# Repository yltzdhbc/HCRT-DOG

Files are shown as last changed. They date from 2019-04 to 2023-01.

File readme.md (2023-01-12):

# 【开源四足机器人】 HCRT-DOG

Jump

**本项目是一个并联式的四足机器人 每条腿使用了两个电机驱动共四条腿，八个电机期望实现四种步态，从慢到快依次为，行进步态（三足支撑）、小跑步态（两拍步态）、溜蹄步态、疾驰步态。**

---

>该软件遵循MIT开源协议，作者保留版权，无任何其他限制，但是你必须在你的软件中包含原MIT授权协议的声明。由于本人时间、能力有限，有许多不足之处，欢迎在GitHub的`Issues`中留言

更多信息请访问：

我的博客：https://yltzdhbc.top/HCRT-DOG

github: https://github.com/yltzdhbc/HCRT-DOG

gitee: https://gitee.com/yltzdhbc/HCRT-DOG

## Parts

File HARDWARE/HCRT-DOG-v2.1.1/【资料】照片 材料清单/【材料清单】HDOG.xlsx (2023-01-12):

序号 | 材料名称 | SW零件标注 | 型号 | 单价（元/个） | 数量（个） | 金额（元） | 备注 | 链接
1 | 塞打螺丝 | 【塞打螺丝】M10-16 | 光杆直径：10mm 光杆长度：16mm 螺纹直径：M8 | 3.95 | 3 | 11.85 |  | https://item.taobao.com/item.htm?spm=a1z10.3-c-s.w4002-17447720939.19.30d73951rLTWwY&id=13899628761
2 | 深沟球轴承 | 【深沟球轴承】6800ZZ 尺寸：10-19-5 | 内径：10mm 外径：19mm 厚度：5mm | 1.4 | 6 | 8.4 |  | https://item.taobao.com/item.htm?spm=a1z10.3-c-s.w4002-17447720939.14.1cba3951MBdidW&id=12451607060
3 | 平面推力滚针轴承 | 【平面推力滚针轴承】尺寸：10-24-4 | 内径：10mm 外径：24mm 厚度：4mm | 2.16 | 3 | 6.48 |  | https://detail.tmall.com/item.htm?id=586222233089&_u=v2mk2m4e0769&skuId=4149740695817
4 | 滑板轴承 | 【深沟球轴承】608ZZ 尺寸：8-22-7 | 内径：8mm 外径：22mm 厚度：7mm | 0.8 | 2 | 1.6 |  | https://item.taobao.com/item.htm?spm=a1z10.3-c-s.w4002-17447720939.12.10843951j3HL8x&id=10864775059
5 | 光轴

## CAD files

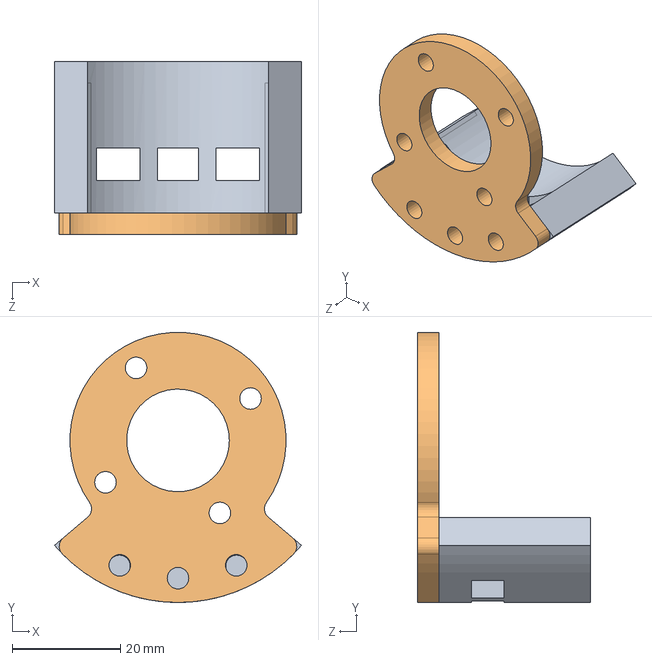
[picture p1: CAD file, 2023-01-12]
HARDWARE/HCRT-DOG-v2.1.1/B【部分装配】马蹄.SLDASM
45.7 x 50.0 x 32.0 mm
【马蹄结构件】蹄子底板
【马蹄结构件】蹄子侧板

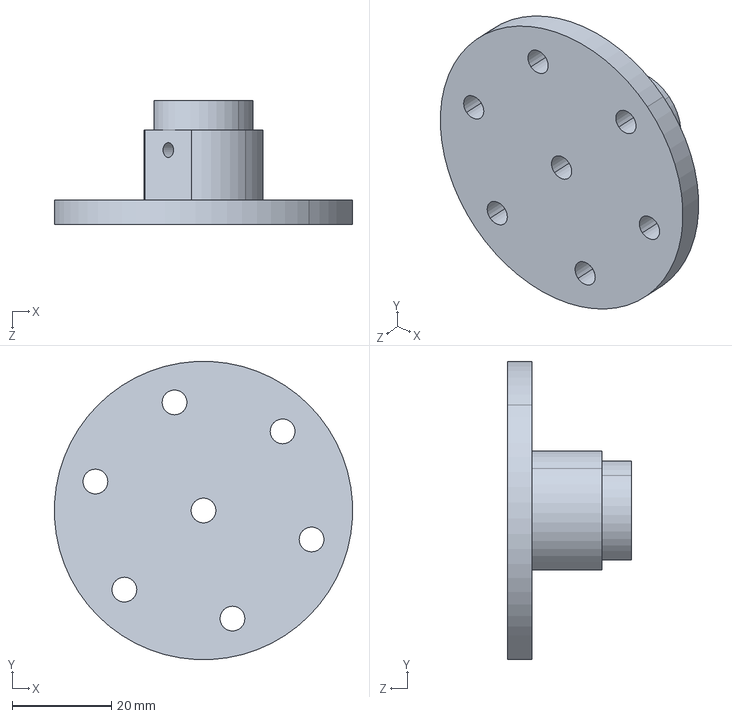
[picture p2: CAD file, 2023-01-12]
HARDWARE/HCRT-DOG-v2.1.1/【法兰联轴器】M10-孔3.SLDASM
59.9 x 59.9 x 25.0 mm

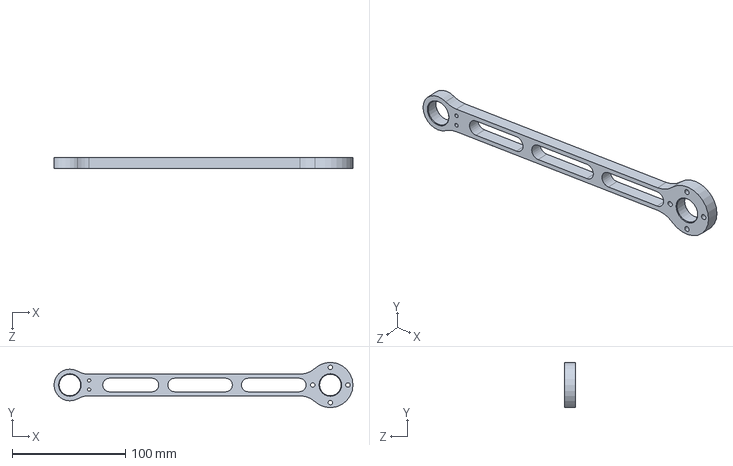
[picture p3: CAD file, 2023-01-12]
HARDWARE/HCRT-DOG-v2.1.1/【铝合金结构件】小腿2.SLDPRT
264.0 x 40.0 x 10.0 mm

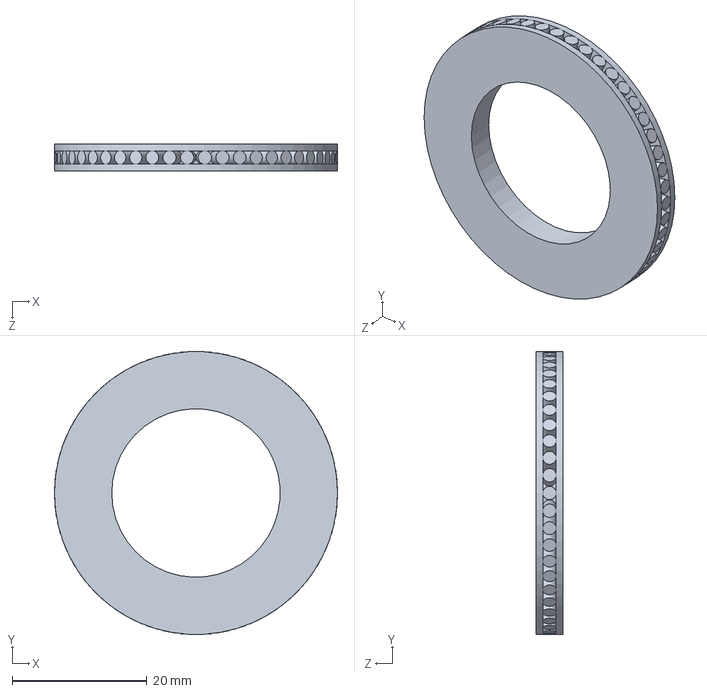
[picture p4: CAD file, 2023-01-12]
HARDWARE/HCRT-DOG-v2.1.1/【平面推力滚针轴承】尺寸：25-42-4.SLDPRT
42.0 x 42.0 x 4.00 mm

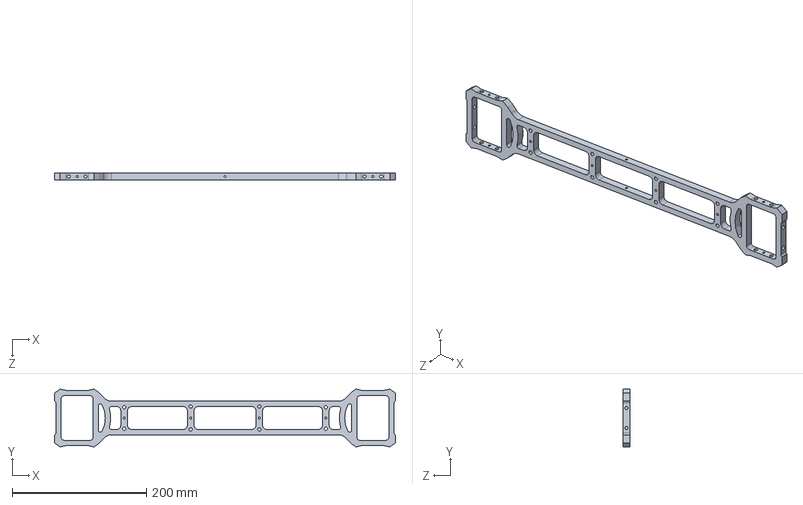
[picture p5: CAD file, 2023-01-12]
HARDWARE/HCRT-DOG-v2.1.1/【铝合金结构件】侧边铝板.SLDPRT
507.2 x 86.2 x 10.0 mm

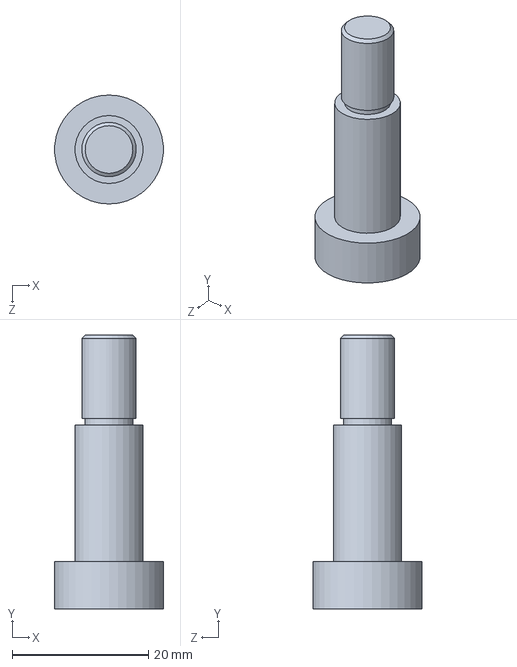
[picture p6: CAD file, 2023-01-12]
HARDWARE/HCRT-DOG-v2.1.1/【塞打螺丝】M10-20.SLDPRT
15.9 x 40.2 x 16.0 mm

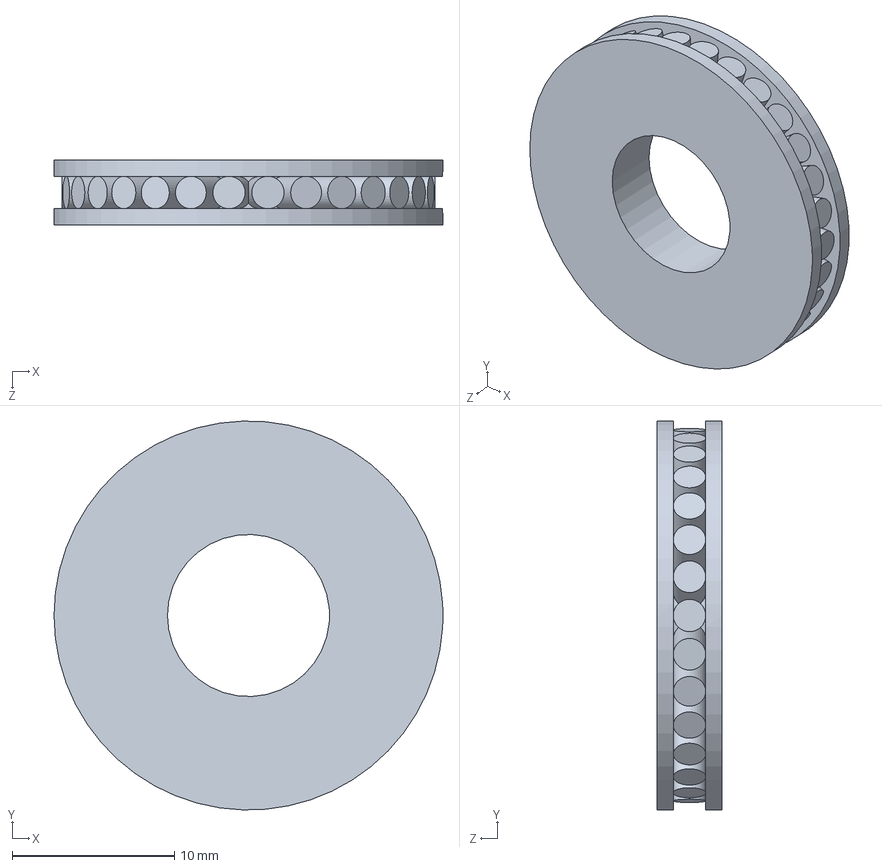
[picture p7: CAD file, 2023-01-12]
HARDWARE/HCRT-DOG-v2.1.1/【平面推力滚针轴承】尺寸：10-24-4.SLDPRT
24.0 x 24.0 x 4.00 mm

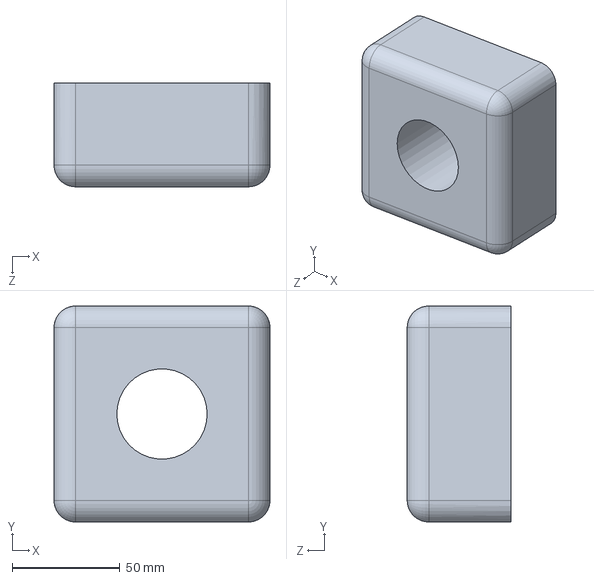
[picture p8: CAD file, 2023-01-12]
HARDWARE/HCRT-DOG-v2.1.1/【泡沫保护件】外侧电机保护泡沫.SLDPRT
100.0 x 100.0 x 48.0 mm

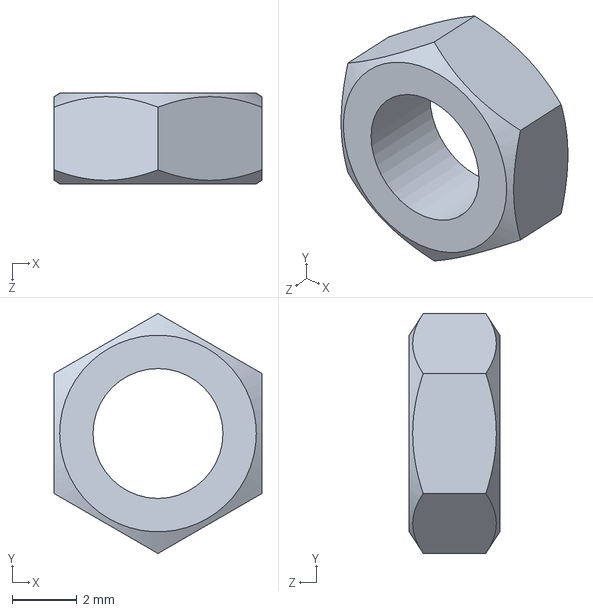
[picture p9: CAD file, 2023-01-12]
HARDWARE/HCRT-DOG-v2.1.1/【螺母】M4-2.8 普通六角螺母.SLDPRT
6.40 x 7.39 x 2.80 mm

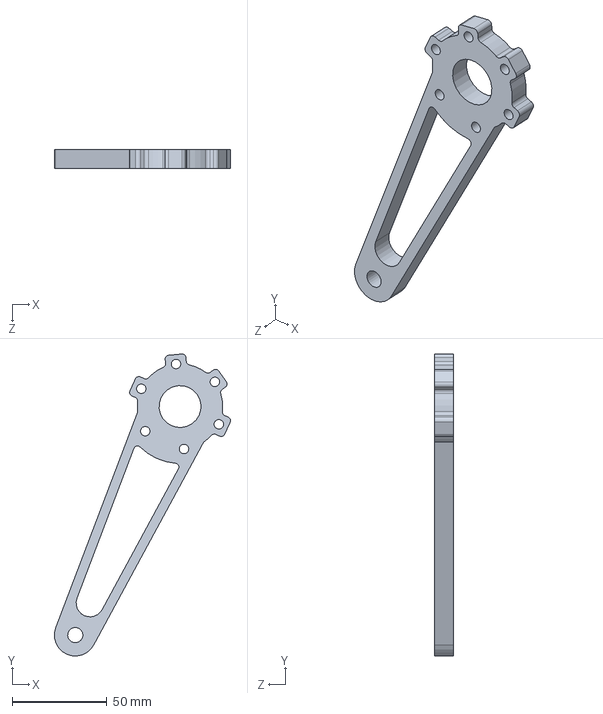
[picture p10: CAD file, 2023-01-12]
HARDWARE/HCRT-DOG-v2.1.1/【铝合金结构件】大腿.SLDPRT
92.9 x 159.3 x 10.0 mm

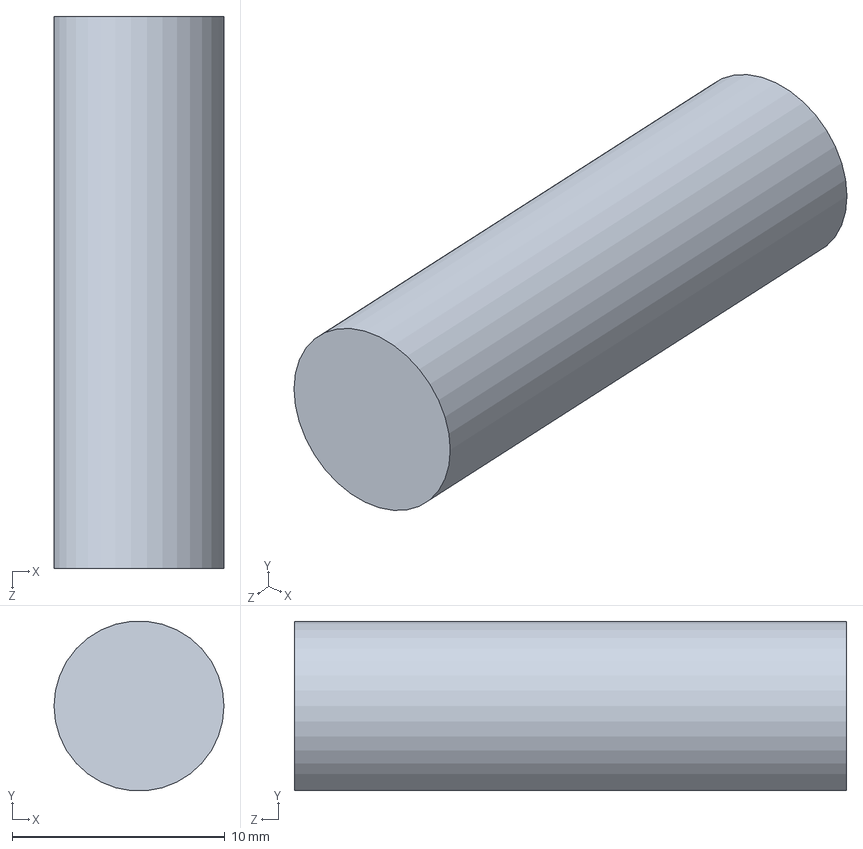
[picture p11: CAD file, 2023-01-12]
HARDWARE/HCRT-DOG-v2.1.1/【光杆】M8-26.SLDPRT
8.00 x 7.97 x 26.0 mm

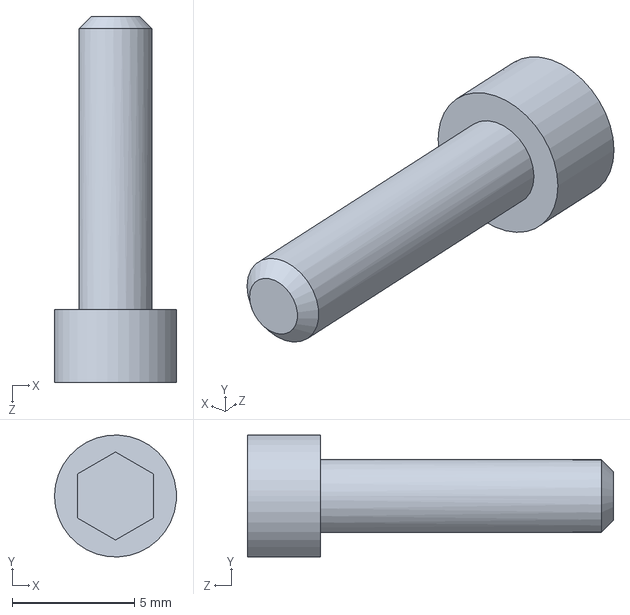
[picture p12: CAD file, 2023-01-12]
HARDWARE/HCRT-DOG-v2.1.1/【螺丝】M3-12 杯头内六角.SLDPRT
5.00 x 4.99 x 15.0 mm

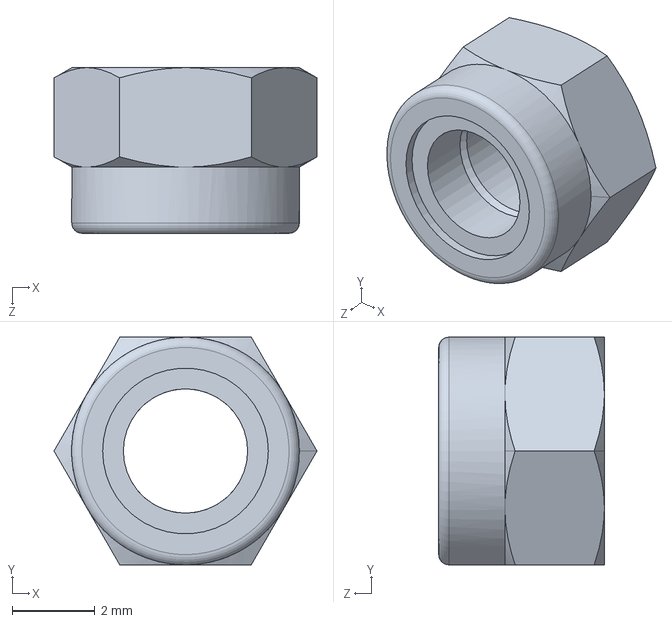
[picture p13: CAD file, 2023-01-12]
HARDWARE/HCRT-DOG-v2.1.1/【螺母】M3-4.0 自锁六角螺母 .SLDPRT
6.35 x 5.50 x 4.00 mm

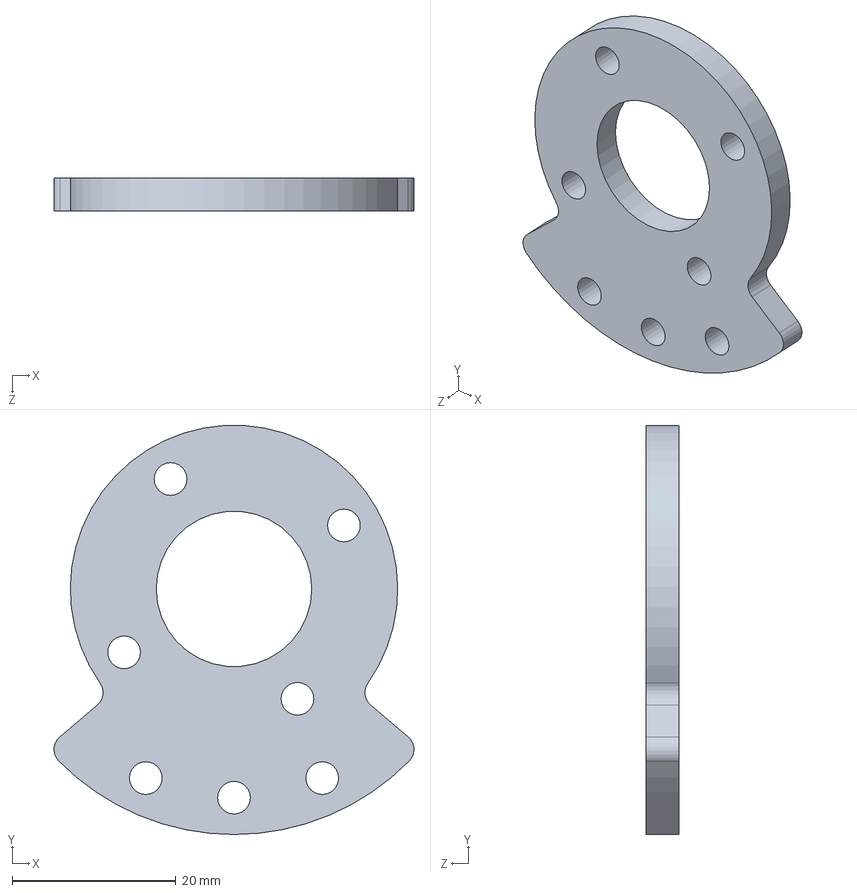
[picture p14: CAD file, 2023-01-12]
HARDWARE/HCRT-DOG-v2.1.1/【马蹄结构件】蹄子侧板.SLDPRT
44.0 x 50.0 x 4.00 mm

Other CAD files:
HARDWARE/HCRT-DOG-v2.1.1/【螺丝】M5-10 杯头内六角.SLDPRT
HARDWARE/HCRT-DOG-v2.1.1/【螺丝】M4-10 杯头内六角.SLDPRT
HARDWARE/HCRT-DOG-v2.1.1/【碳纤维板垫片】10-15-2.SLDPRT
HARDWARE/HCRT-DOG-v2.1.1/【螺丝】M3-22 杯头内六角.SLDPRT
HARDWARE/HCRT-DOG-v1.0.3/1.SLDASM
HARDWARE/HCRT-DOG-v1.0.3/10cm.SLDPRT
HARDWARE/HCRT-DOG-v1.0.3/2.SLDASM
HARDWARE/HCRT-DOG-v1.0.3/20-1.SLDPRT
HARDWARE/HCRT-DOG-v1.0.3/20cm.SLDPRT
HARDWARE/HCRT-DOG-v1.0.3/3508电机.SLDASM
HARDWARE/HCRT-DOG-v1.0.3/RM3508电机.sldprt
HARDWARE/HCRT-DOG-v1.0.3/减震橡胶.SLDPRT
HARDWARE/HCRT-DOG-v1.0.3/吸盘夹/changganjiachi.SLDPRT
HARDWARE/HCRT-DOG-v1.0.3/吸盘夹/一号彭磊机构总装.SLDASM
HARDWARE/HCRT-DOG-v1.0.3/吸盘夹/升降机构铝板.SLDPRT
HARDWARE/HCRT-DOG-v1.0.3/吸盘夹/吸盘.SLDPRT
HARDWARE/HCRT-DOG-v1.0.3/吸盘夹/吸盘夹.SLDASM
HARDWARE/HCRT-DOG-v1.0.3/吸盘夹/吸盘板.SLDPRT
HARDWARE/HCRT-DOG-v1.0.3/吸盘夹/吸盘板12个吸盘.DWG
HARDWARE/HCRT-DOG-v1.0.3/吸盘夹/吸盘，内径16.SLDASM
HARDWARE/HCRT-DOG-v1.0.3/吸盘夹/小细管.SLDPRT
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

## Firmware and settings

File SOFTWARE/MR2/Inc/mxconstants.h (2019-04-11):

/**
  ******************************************************************************
  * File Name          : mxconstants.h
  * Description        : This file contains the common defines of the application
  ******************************************************************************
  *
  * COPYRIGHT(c) 2017 STMicroelectronics
  *
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
  ******************************************************************************
  */
/* Define to prevent recursive inclusion -------------------------------------*/
#ifndef __MXCONSTANT_H
#define __MXCONSTANT_H
  /* Includes ------------------------------------------------------------------*/


#define IST_INT_Pin GPIO_PIN_3
#define IST_INT_GPIO_Port GPIOE
#define IST_RST_Pin GPIO_PIN_2
#define IST_RST_GPIO_Port GPIOE
#define IMU_HEAT_PWM_Pin GPIO_PIN_5
#define IMU_HEAT_PWM_GPIO_Port GPIOB
#define LASER_Pin GPIO_PIN_13
#define LASER_GPIO_Port GPIOG
#define BEEP_Pin GPIO_PIN_4
#define BEEP_GPIO_Port GPIOB
#define KEY1_Pin GPIO_PIN_7
#define KEY1_GPIO_Port GPIOD
#define KEY2_Pin GPIO_PIN_10
#define KEY2_GPIO_Port GPIOD
#define LED1_Pin GPIO_PIN_14
#define LED1_GPIO_Port GPIOF
#define LED2_Pin GPIO_PIN_7
#define LED2_GPIO_Port GPIOE
/**
  * @}
  */ 

/**
  * @}
*/ 

#endif /* __MXCONSTANT_H */
/************************ (C) COPYRIGHT STMicroelectronics *****END OF FILE****/

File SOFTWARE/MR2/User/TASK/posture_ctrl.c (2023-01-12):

#include "posture_ctrl.h"


float x, y, theta1, theta2;

enum States state = REALSE;

extern TaskHandle_t MotorControlTask_Handler;

float _angle_initial,_rotate_angle;

bool TurnLeftFlag1,TurnLeftFlag2,TurnRightFlag1,TurnRightFlag2,ClimbingFlag1,ClimbingFlag2;

bool _leg_active[4]= {1,1,1,1};

float now_time;

bool rc_ctrl_flag = 1;

//初始化步态增益
LegGain gait_gains = {15.5, 0.00, 25.0, 0.00};
//设定每一种步态的具体增益
LegGain state_gait_gains[] = {
    //{kp_pos, kd_pos} kp_spd, kd_spd,
    {22.0, 0.00, 8.0, 0.00},  //位置环 速度环 TROT
    {22.0, 0.00, 8.0, 0.00},  //TEST1
    {22.0, 0.00, 8.0, 0.00},
    {22.0, 0.00, 8.0, 0.00},
    {22.0, 0.00, 8.0, 0.00},
    {22.0, 0.00, 8.0, 0.00},
    {22.0, 0.00, 8.0, 0.00},
    {22.0, 0.00, 8.0, 0.00},
    {22.0, 0.00, 8.0, 0.00},
    {22.0, 0.00, 8.0, 0.00},
    {22.0, 0.00, 8.0, 0.00},
    {22.0, 0.00, 8.0, 0.00},
    {22.0, 0.00, 8.0, 0.00},  //TEST12
    {22.0, 0.00, 8.0, 0.00},  //CLIMB
    {22.0, 0.00, 8.0, 0.00},
    {22.0, 0.00, 8.0, 0.00},
    {22.0, 0.00, 8.0, 0.00},
    {22.0, 0.00, 8.0, 0.00},
    {22.0, 0.00, 8.0, 0.00},
    {22.0, 0.00, 8.0, 0.00},
    {22.0, 0.00, 8.0, 0.00}, //STOP
    {22.0, 0.00, 8.0, 0.00}, //REL
    {22.0, 0.00, 8.0, 0.00},
    {22.0, 0.00, 8.0, 0.00},
    {22.0, 0.00, 8.0, 0.00},
};


//初始化步态参数
GaitParams gait_params = {17.3,12.0,4.0,0.00,0.25,1};
//设定每一种步态的具体参数
GaitParams state_gait_params[] = {
    //{stance_height, step_length, up_amp, down_amp, flight_percent, freq}  cm
    //{步高, 步长, 抬腿高, 压腿高, 飞行占比, 频率}	单位 cm
    {16.0, 16.0, 5.00, 2.00, 0.25, 1.85}, // TROT	双拍步态 对角小跑
    {26.0, 10.00, 3, 2.00, 0.20, 2.0},//1
    {26.0, 10.00, 3, 2.00, 0.20, 2.0},//2
    {26.0, 10.00, 3, 2.00, 0.20, 2.0},//3
    {NAN, NAN, NAN, NAN, NAN, NAN},		//4
    {NAN, NAN, NAN, NAN, NAN, NAN},		//5
    {NAN, NAN, NAN, NAN, NAN, NAN},		//6
    {NAN, NAN, NAN, NAN, NAN, NAN},		//7
    {NAN, NAN, NAN, NAN, NAN, NAN},		//8
    {NAN, NAN, NAN, NAN, NAN, NAN},		//9
    {NAN, NAN, NAN, NAN, NAN, NAN},		//10
    {NAN, NAN, NAN, NAN, NAN, NAN},		//11
    {NAN, NAN, NAN, NAN, NAN, NAN},		//12

    {16.3, 0.00, 5.70, 3.00, 0.30, 2.8}, // CLIMBING	爬坡

    {16.3, 0.00, 6.0, 0.00, 2.5, 1.5}, // WALK
    {16.0, 8.00, 5.00, 0.00, 0.30, 1.2}, // WALK BACK

    {23.0, 7.00, 3, 2.00, 0.25, 3.0}, // ROTATE LEFT			{23.0, 10.00, 3, 2.00, 0.20, 2.0},  {21.0, 16.0, 5.00, 3.00, 0.25, 2.3},
    {21.0, 7.00, 5, 2.00, 0.25, 3.0},	// ROTATE RIGHT			{23.0, 10.00, 3, 2.00, 0.20, 2.0},

    {17.0, 0.00, 6.00, 4.00, 0.35, 2.0}, //BOUND
    {17.0, 0.00, 6.00, 0.00, 0.35, 2.0}, // GALLOP

    {NAN, NAN, NAN, NAN, NAN, NAN}, // STOP
    {NAN, NAN, NAN, NAN, NAN, NAN}, // RELASE
    {NAN, NAN, NAN, NAN, NAN, NAN}, // JUMP
    {NAN, NAN, NAN, NAN, NAN, NAN}, // START
    {NAN, NAN, NAN, NAN, NAN, NAN}, // END

    {25.3, 16.0, 15.00, 0.00, 0.30, 1.2} // TEST
};


/**
*	最低walk {12.0, 15.0, 1.8, 0.00, 0.50, 1.0}
*	效果不错{14.0, 12.0, 3.5, 0.00, 0.50, 1.0},
*	{16.0, 12.00, 5.0, 0.00, 0.20, 2.0}, // WALK		ahead 不错
*	{17.3, 12.00, 4.0, 0.00, 0.35, 2.5}, // WALK		ahead
* 对角小跑步态不错速度和稳定都非常好
*/

GaitParams test_gait_params= {16.0, 15.0, 5.00, 2.00, 0.25, 2.3}; // TROT		//双拍步态 对角小跑
LegGain test_gait_gains= {15.5, 0.00, 25.0, 0.00};


const float TROT_stance_height=26.0;
const float TROT_step_length=25.0;
const float TROT_up_amp=15.2;
const float TROT_down_amp=0.0;
const float TROT_flight_percent=0.20;
const float TROT_freq=0.2;

const float TROT_step_length2=25.0;
const float TROT_up_amp2=15.2;


//        {26.0, 25.00, 15.0, 0.00, 0.20, 0.2},
//        {26.0, 25.00, 15.0, 0.00, 0.20, 0.2},

//        {26.0, 25.00-15, 15.0-13, 0.00, 0.20, 0.2},
//        {26.0, 25.00-15, 15.0-13, 0.00, 0.20, 0.2}


DetachedParam detached_params;
DetachedParam state_detached_params[] = {

    {   //TROT 对角小跑
        {21.0, 14.0, 3.00, 2.00, 0.25, 4.0},  //   {21.0, 12.0, 3.00, 2.00, 0.25, 4.0}
        {21.0, 14.0, 3.00, 2.00, 0.25, 4.0},
        {21.0, 14.0, 3.00, 2.00, 0.25, 4.0},
        {21.0, 14.0, 3.00, 2.00, 0.25, 4.0}
    },
    {   // TEST1
        {25.0, 10.00, 3, 2.00, 0.25, 3.8},
        {25.0, 10.00, 3, 2.00, 0.25,3.8},

        {25.0, 10.00, 3, 2.00, 0.25, 3.8},
        {25.0, 10.00, 3, 2.00, 0.25, 3.8}
    },
    {   //TEST2
        {28.0, 25.00, 17, 0.00, 0.49, 0.4},
        {28.0, 25.00, 17, 0.00, 0.49, 0.4},

        {28.0, 12.00, 4, 0.00, 0.49, 0.4},
        {28.0, 12.00, 4, 0.00, 0.49, 0.4}
    },
    {   //TEST3
        {28.0, 12.00, 2, 0.00, 0.49, 0.4},
        {28.0, 12.00, 2, 0.00, 0.49, 0.4},

        {28.0, 20.00, 17, 0.00, 0.48, 0.4},
        {28.0, 20.00, 17, 0.00, 0.48, 0.4},
    },
    {   // TEST4
        {17.5, 14.00, 4, 0.00, 0.25, 2.0},
        {17.5, 14.00, 4, 0.00, 0.25,2.0},

        {20.5, 14.00, 4, 0.00, 0.25, 2.0},
        {20.5, 14.00, 4, 0.00, 0.25, 2.0}
    },
    {   // TEST5
        {23.0, 18.00, 6, 1.00, 0.25, 2.0},
        {23.0, 18.00, 6, 1.00, 0.25, 2.0},

        {16.0, 10.00, 3, 1.00, 0.25, 2.0},
        {16.0, 10.00, 3, 1.00, 0.25,2.0},
    },
    {   // TEST6
        {26.0, 6.00, 3, 0.00, 0.25, 3.0},
        {26.0, 6.00, 3, 0.00, 0.25,3.0},

        {26.0, 6.00, 3, 0.00, 0.25, 3.0},
        {26.0, 6.00, 3, 0.00, 0.25, 3.0}
    },
    {   // TEST7       //调整方向 小碎步转弯 左
        {26.0, 8.0, 4.00, 3.00, 0.25, 2.1},
        {26.0, 8.0, 4.00, 3.00, 0.25, 2.1},
        {26.0, 8.0, 4.00, 3.00, 0.25, 2.1},
        {26.0, 8.0, 4.00, 3.00, 0.25, 2.1}
    },
    {   // TEST8			//调整方向 小碎步转弯 右
        {26.0, 8.0, 4.00, 3.00, 0.25, 2.1},
        {26.0, 8.0, 4.00, 3.00, 0.25, 2.1},
        {26.0, 8.0, 4.00, 3.00, 0.25, 2.1},
        {26.0, 8.0, 4.00, 3.00, 0.25, 2.1}
    },
    {   // TEST9
        {28.0, 4.00, 3, 0.00, 0.25, 2.3},
        {28.0, 4.00, 3, 0.00, 0.25,2.3},

        {28.0, 4.00, 3, 0.00, 0.25, 2.3},
        {28.0, 4.00, 3, 0.00, 0.25, 2.3}
    },
    {   // TEST10
        {28.0, 4.00, 3, 0.00, 0.25, 2.3},
        {28.0, 4.00, 3, 0.00, 0.25,2.3},

        {28.0, 4.00, 3, 0.00, 0.25, 2.3},
        {28.0, 4.00, 3, 0.00, 0.25, 2.3}
    },
    {   // TEST11
        {28.0, 4.00, 3, 0.00, 0.25, 2.3},
        {28.0, 4.00, 3, 0.00, 0.25,2.3},

        {28.0, 4.00, 3, 0.00, 0.25, 2.3},
        {28.0, 4.00, 3, 0.00, 0.25, 2.3}
    },
    {   // TEST12
        {20.3, 30.00, 5.70, 3.00, 0.44, 2.8},
        {20.3, 30.00, 5.70, 3.00, 0.44, 2.8},

        {20.3, 30.00, 5.70, 3.00, 0.44, 2.8},
        {20.3, 30.00, 5.70, 3.00, 0.44, 2.8},
    },

    {   //CLIMBING	爬坡

        {16.0, 9.0, 3.00, 1.00, 0.25, 3.6},		//小步子可以迈上去
        {16.0, 9.0, 3.00, 1.00, 0.25, 3.6},

        {18.0, 9.0, 3.00, 1.00, 0.25, 3.6},
        {18.0, 9.0, 3.00, 1.00, 0.25, 3.6}
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

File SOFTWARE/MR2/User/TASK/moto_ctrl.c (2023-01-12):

#include "moto_ctrl.h"

void send_chassis_cur1_4(int16_t motor1, int16_t motor2, int16_t motor3, int16_t motor4);
void send_chassis_cur5_8(int16_t motor5, int16_t motor6, int16_t motor7, int16_t motor8);

bool IsMotoReadyOrNot= NotReady;
float ref_agle[8]= {0};
float temp_angle;
temp_data temp_pid= {0};     //pid中间数据

float test_speed=0;
u16 pid_spd_out_limit = 6720;
/*******************************************************************************************
	*@ 函数名称：void MotorControl_task(void *pvParameters)
	*@ 功能： 接受电机反馈数据并且进行PID计算 输出电流大小控制电机位置
	*@ 备注： FREERTOS任务函数
 *******************************************************************************************/
void MotorControl_task(void *pvParameters)
{
    for(;;) {
        moto_behaviour();
    }

}

void moto_behaviour(void)
{
    if(IsMotoReadyOrNot== IsReady) {
        for(int i=0; i<8; i++)
            ref_agle[i]=temp_pid.ref_agle[i];
        IsMotoReadyOrNot= NotReady;
    }

    for(int i=0; i<8; i++) {

        //pid_calc(&pid_pos[i],moto_chassis[i].total_angle/100,ref_agle[i]/100);  //位置环 角度控制
        pid_calc(&pid_pos[i],moto_chassis[i].total_angle*360/8191,ref_agle[i]*360/8191);  //位置环 角度控制

        if(pid_pos[i].pos_out>pid_spd_out_limit)pid_pos[i].pos_out=pid_spd_out_limit;	//最高速度限制
        else if(pid_pos[i].pos_out<-pid_spd_out_limit)pid_pos[i].pos_out=-pid_spd_out_limit; //最高速度限制

        //temp_pid.out[i] = pid_calc(&pid_spd[i],moto_chassis[i].speed_rpm,test_speed);  //速度环 测试
        //temp_pid.out[i] = pid_calc(&pid_spd[i],moto_chassis[i].speed_rpm,pid_pos[i].pos_out);  //速度环 速度控制
        moto_chassis[i].given_current = pid_calc(&pid_spd[i],moto_chassis[i].speed_rpm,pid_pos[i].pos_out);  //速度环 速度控制
    }

    send_chassis_cur5_8(moto_chassis[4].given_current,moto_chassis[5].given_current,moto_chassis[6].given_current,moto_chassis[7].given_current);		//传递5-8数据给can收发器
    send_chassis_cur1_4(moto_chassis[0].given_current,moto_chassis[1].given_current,moto_chassis[2].given_current,moto_chassis[3].given_current);		//传递1-4数据给can收发器

    osDelay(3);		//控制频率  给	1	7号和8号电机会失控

}

/**
* NAME: void pid_param_init(void)
* FUNCTION : pid参数填充初始化
*/
void pid_param_init(void)
{

    for (int i = 0; i < 8; i++)//  						20,0.01,0  37,0.008   8.0f, 0.000f   16
        PID_struct_init(&pid_pos[i], POSITION_PID, 100000.0f, 2000.0f, 8.0f, 0.0008f, 0.0f);  //位置环PID参数设置（pid结构体，PID类型，最大输出，比例限制，P , I , D ）

    for (int i = 0; i < 8; i++)  //									16384.0f对应20A					15.5f,0,0 // 16.0f, 0.001f   20.0f, 0.004297f   22.0f, 0.01399f
        PID_struct_init(&pid_spd[i], POSITION_PID, 16000.0f, 2000.0f, 15.5f, 0.000100, 0.0f);		//速度环PID（pid结构体，PID类型，最大输出，比例限制，P , I , D ）
    //20.0f, 0.004297f, 0.0f     22.0f, 0.001

    PID_struct_init(&pid_imu[0], POSITION_PID, 10000, 0, 1.5f, 0.01, 0);		//roll

    PID_struct_init(&pid_imu[1], POSITION_PID, 10000, 0, 1.5f, 0.01, 0);		//pitch

    PID_struct_init(&pid_imu[2], POSITION_PID, 10000, 0, 1.30f, 0, 0);		//yaw

    PID_struct_init(&pid_climbing, POSITION_PID, 10000, 10000, 3.5f, 0, 0);		//yaw 1.8

    PID_struct_init(&pid_test1, POSITION_PID, 10000, 0, 1.5f, 0, 0);		//yaw

    PID_struct_init(&pid_openmv_dev, POSITION_PID, 10000, 0, 1.5f, 0, 0);		//yaw
}

//发送底盘电机控制命令
void send_chassis_cur1_4(int16_t motor1, int16_t motor2, int16_t motor3, int16_t motor4)
{
    hcan1.pTxMsg->StdId   = 0x200;
    hcan1.pTxMsg->IDE     = CAN_ID_STD;
    hcan1.pTxMsg->RTR     = CAN_RTR_DATA;
    hcan1.pTxMsg->DLC     = 0x08;
    hcan1.pTxMsg->Data[0] = motor1 >> 8;
    hcan1.pTxMsg->Data[1] = motor1;
    hcan1.pTxMsg->Data[2] = motor2 >> 8;
    hcan1.pTxMsg->Data[3] = motor2;
    hcan1.pTxMsg->Data[4] = motor3 >> 8;
    hcan1.pTxMsg->Data[5] = motor3;
    hcan1.pTxMsg->Data[6] = motor4 >> 8;
    hcan1.pTxMsg->Data[7] = motor4;
    HAL_CAN_Transmit(&hcan1, 10);
}

//发送底盘电机控制命令
void send_chassis_cur5_8(int16_t motor5, int16_t motor6, int16_t motor7, int16_t motor8)
{
    hcan1.pTxMsg->StdId   = 0x1ff;
    hcan1.pTxMsg->IDE     = CAN_ID_STD;
    hcan1.pTxMsg->RTR     = CAN_RTR_DATA;
    hcan1.pTxMsg->DLC     = 0x08;
    hcan1.pTxMsg->Data[0] = motor5 >> 8;
    hcan1.pTxMsg->Data[1] = motor5;
    hcan1.pTxMsg->Data[2] = motor6 >> 8;
    hcan1.pTxMsg->Data[3] = motor6;
    hcan1.pTxMsg->Data[4] = motor7 >> 8;
    hcan1.pTxMsg->Data[5] = motor7;
    hcan1.pTxMsg->Data[6] = motor8 >> 8;
    hcan1.pTxMsg->Data[7] = motor8;
    HAL_CAN_Transmit(&hcan1, 10);
}

void Lm298n_pin_init(void)
{

    GPIO_InitTypeDef GPIO_InitStruct;
    GPIO_InitStruct.Pin = GPIO_PIN_0|GPIO_PIN_1;
    GPIO_InitStruct.Mode = GPIO_MODE_OUTPUT_PP;
    GPIO_InitStruct.Pull = GPIO_NOPULL;
    GPIO_InitStruct.Speed = GPIO_SPEED_FREQ_LOW;
    HAL_GPIO_Init(GPIOF, &GPIO_InitStruct);

}


void Lm298n_ctrl( int  mode )
{

    if(mode==Lm298n_break)
    {
        HAL_GPIO_WritePin(GPIOF,GPIO_PIN_1,GPIO_PIN_SET);
        HAL_GPIO_WritePin(GPIOF,GPIO_PIN_0,GPIO_PIN_SET);
    }
    else if(mode==Lm298n_forward)
    {
        HAL_GPIO_WritePin(GPIOF,GPIO_PIN_1,GPIO_PIN_RESET);
        HAL_GPIO_WritePin(GPIOF,GPIO_PIN_0,GPIO_PIN_SET);
    }
    else if(mode==Lm298n_backward)
    {
        HAL_GPIO_WritePin(GPIOF,GPIO_PIN_1,GPIO_PIN_SET);
        HAL_GPIO_WritePin(GPIOF,GPIO_PIN_0,GPIO_PIN_RESET);
    }


}

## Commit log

2023-01-12 Upload the entire project
    [1.SLDASM, 10cm.SLDPRT, 2.SLDASM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]
2023-01-12 upload v2 structure
    [1.SLDASM, 10cm.SLDPRT, 2.SLDASM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]
